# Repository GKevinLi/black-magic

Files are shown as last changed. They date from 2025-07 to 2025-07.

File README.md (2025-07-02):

# Black Magic: A Brushless DC Motor Driver



This is a custom 4S 20A Sensorless BLDC Motor Driver designed for drone motor operation. I haven't had time to make the drone itself because I spent all my time designing this custom PCB instead. Still worth it though.

Features a DRV8323 motor driver chip along with a STM32 microcontroller. Supports full sensorless brushless DC motor operation through PWM input along with current sensing. 

It's called Black Magic because, let's be honest here, I'm messing around with powers beyond my comprehension. I'll be lucky if this thing doesn't blow up the first time I try to plug it in, although I've done my best to make sure that doesn't happen. 20A is still way too much current for someone like me to be playing around with.

This took way longer to make than the other one.... i think its obvious why

## Features
- DRV8323 Motor Controller chip
- STM32 Microcontroller
- USB-C port for programming
- PWM Input
- BEMF Detection through a virtual neutral point
- Current Sensing capabilities
- Voltage Regulator for 3.3v power













## BOM

| Item  | Usage | Source  | Price | Quantity | LCSC ID|
| ----| ----|----|----|----|----|
| 100 uf electrolytic capaciator | Bulk Capacitance | JLCPCB | $4.65 | 20 | C7272127 |
| 10 uf capaciator | Capacitance | JLCPCB | $0.08 | 15 | C19702 |
| 3.3 nf capaciator | Capacitance | JLCPCB | $0.10 | 20 | C26404 |
| 100 nf capaciator | Capacitance | JLCPCB | $0.04 | 40 | C1525 |
| 22 uf capaciator | Bulk Capacitance | JLCPCB | $5.25 | 25 | C5189846 |
| 22 uf capaciator (0603 footprint) | Capacitance | JLCPCB | $0.09 | 10 | C59461 |
| 2.2 uf capaciator | Capacitance | JLCPCB | $0.01 | 5 | C12530 |
| 1 uf capaciator | Capacitance | JLCPCB | $0.02 | 5 | C52923 |
| 47 nf capaciator | Capacitance | JLCPCB | $0.04 | 20 | C272875 |
| Schottky Diode | Preventing reverse current | JLCPCB | $0.10 | 10 | C191023 |
| Red LED | Indication | JLCPCB | $0.03 | 5 | C2286 |
| USB C Receptacle | Programming + Power | JLCPCB | $0.30 | 6 | C2927038 |
| MOSFET | Motor Control | JLCPCB | $8.06 | 30 | C201632 |
| 10 ohm resistor | Resistance | JLCPCB | $0.02 | 30 | C25077 |
| 33k ohm resistor | Resistance | JLCPCB | $0.02 | 30 | C25779 |
| 68k ohm resistor | Resistance | JLCPCB | $0.01 | 30 | C36871 |
| 22k ohm resistor | Resistance | JLCPCB | $0.01 | 5 | C25768 |
| 100k ohm resistor | Resistance | JLCPCB | $0.01 | 5 | C25741 |
| 10k ohm resistor | Resistance | JLCPCB | $0.01 | 20 | C25741 |
| 5.1k ohm resistor | Resistance | JLCPCB | $0.01 | 15 | C25905 |
| 0.01 ohm shunt resistor | Shunt Resistance | JLCPCB | $1.05 | 19 | C393070 |
| 4.7k ohm resistor | Resistance | JLCPCB | $0.01 | 5 | C25900 |
| Button | Button | JLCPCB | $0.42 | 10 | C720477 |
| STM32 | Microcontroller | JLCPCB | $15.86 | 5 | C529355 |
| USBLC6 | USB Data Protector | JLCPCB | $0.96 | 5 | C15999 |
| TLV76133 | Voltage Regulator | JLCPCB | $1.10 | 5 | C7527500 |
| DRV8323 | Motor driver | JLCPCB | $13.29| 5 | C7527500 |
| TPS82130 | Buck Converter | JLCPCB | $6.35 | 5 | C473914 |

Total JLCPCB Assmebly Cost: $73.70

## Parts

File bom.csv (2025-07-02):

Designator | Footprint | Quantity | Value | LCSC ID
C1, C10 | CP_Elec_6.3x7.7 | 2 | 100uf | C7272127
C11, C23, C26 | 0603 | 3 | 10uf | C19702
C12 | 0402 | 1 | 3.3nf | C26404
C13, C19, C20, C21 | 0402 | 4 | 100nf | C1525
C14, C15, C16, C17, C18 | 1812 | 5 | 22uf | C5189846
C2, C7 | 0603 | 2 | 22uf | C59461
C22 | 0402 | 1 | 2.2uf | C12530
C24, C25 | 0402 | 2 | 0u1f | C1525
C3, C6 | 0402 | 2 | 0.1uf | C1525
C4 | 0402 | 1 | 1uf | C52923
C5 | 0402 | 1 | 47nf | C272875
D2, D7 | D_SOD-323 | 2 | D_Schottky | C191023
D6 | 0603 | 1 | LED | C2286
J1 | USB_C_Receptacle_HCTL_HC-TYPE-C-16P-01A | 1 | USB_C_Receptacle_USB2.0_14P | C2927038
J2 | PinSocket_1x03_P2.54mm_Vertical | 1 | Conn_01x03 | Not Assembling
J3 | SolderWire-4sqmm_1x02_P12mm_D3mm_OD6mm | 1 | Conn_01x02 | Not Assembling
J4 | SolderWire-4sqmm_1x03_P12mm_D3mm_OD6mm | 1 | Conn_01x03 | Not Assembling
Q1, Q2, Q3, Q4, Q5, Q6 | VSON-8_3.3x3.3mm_P0.65mm_NexFET | 6 | CSD17577Q3A | C201632
R1, R10, R2, R7, R8, R9 | 0402 | 6 | 10 | C25077
R11, R15, R16, R20, R21, R22 | 0402 | 6 | 33k | C25779
R12 | 0402 | 1 | 68k | C36871
R13 | 0402 | 1 | 22k | C25768
R14 | 0402 | 1 | 100k | C25741
R17, R18, R19, R28 | 0402 | 4 | 10k | C25744
R23 | 0402 | 1 | 5.1k | C25905
R24, R25, R26 | 2512 | 3 | 0.01 | C393070
R27 | 0402 | 1 | 4.7k | C25900
R5, R6 | 0402 | 2 | 5k1 | C25905
SW1, SW3 | SW_Push_SPST_NO_Alps_SKRK | 2 | SW_Push | C720477
U1 | LQFP-48_7x7mm_P0.5mm | 1 | STM32G431CBTx | C529355
U3 | SOT-666 | 1 | USBLC6-2P6 | C15999
U4 | SOT-223-3_TabPin2 | 1 | TLV76133DCY | C7527500
U8 | QFN50P600X600X80-41N415X415 | 1 | DRV8323SRTAT | C2150452
U9 | Texas_SIL0008D_MicroSiP-8-1EP_2.8x3mm_P0.65mm_EP1.1x1.9mm_ThermalVias | 1 | TPS82130 | C473914

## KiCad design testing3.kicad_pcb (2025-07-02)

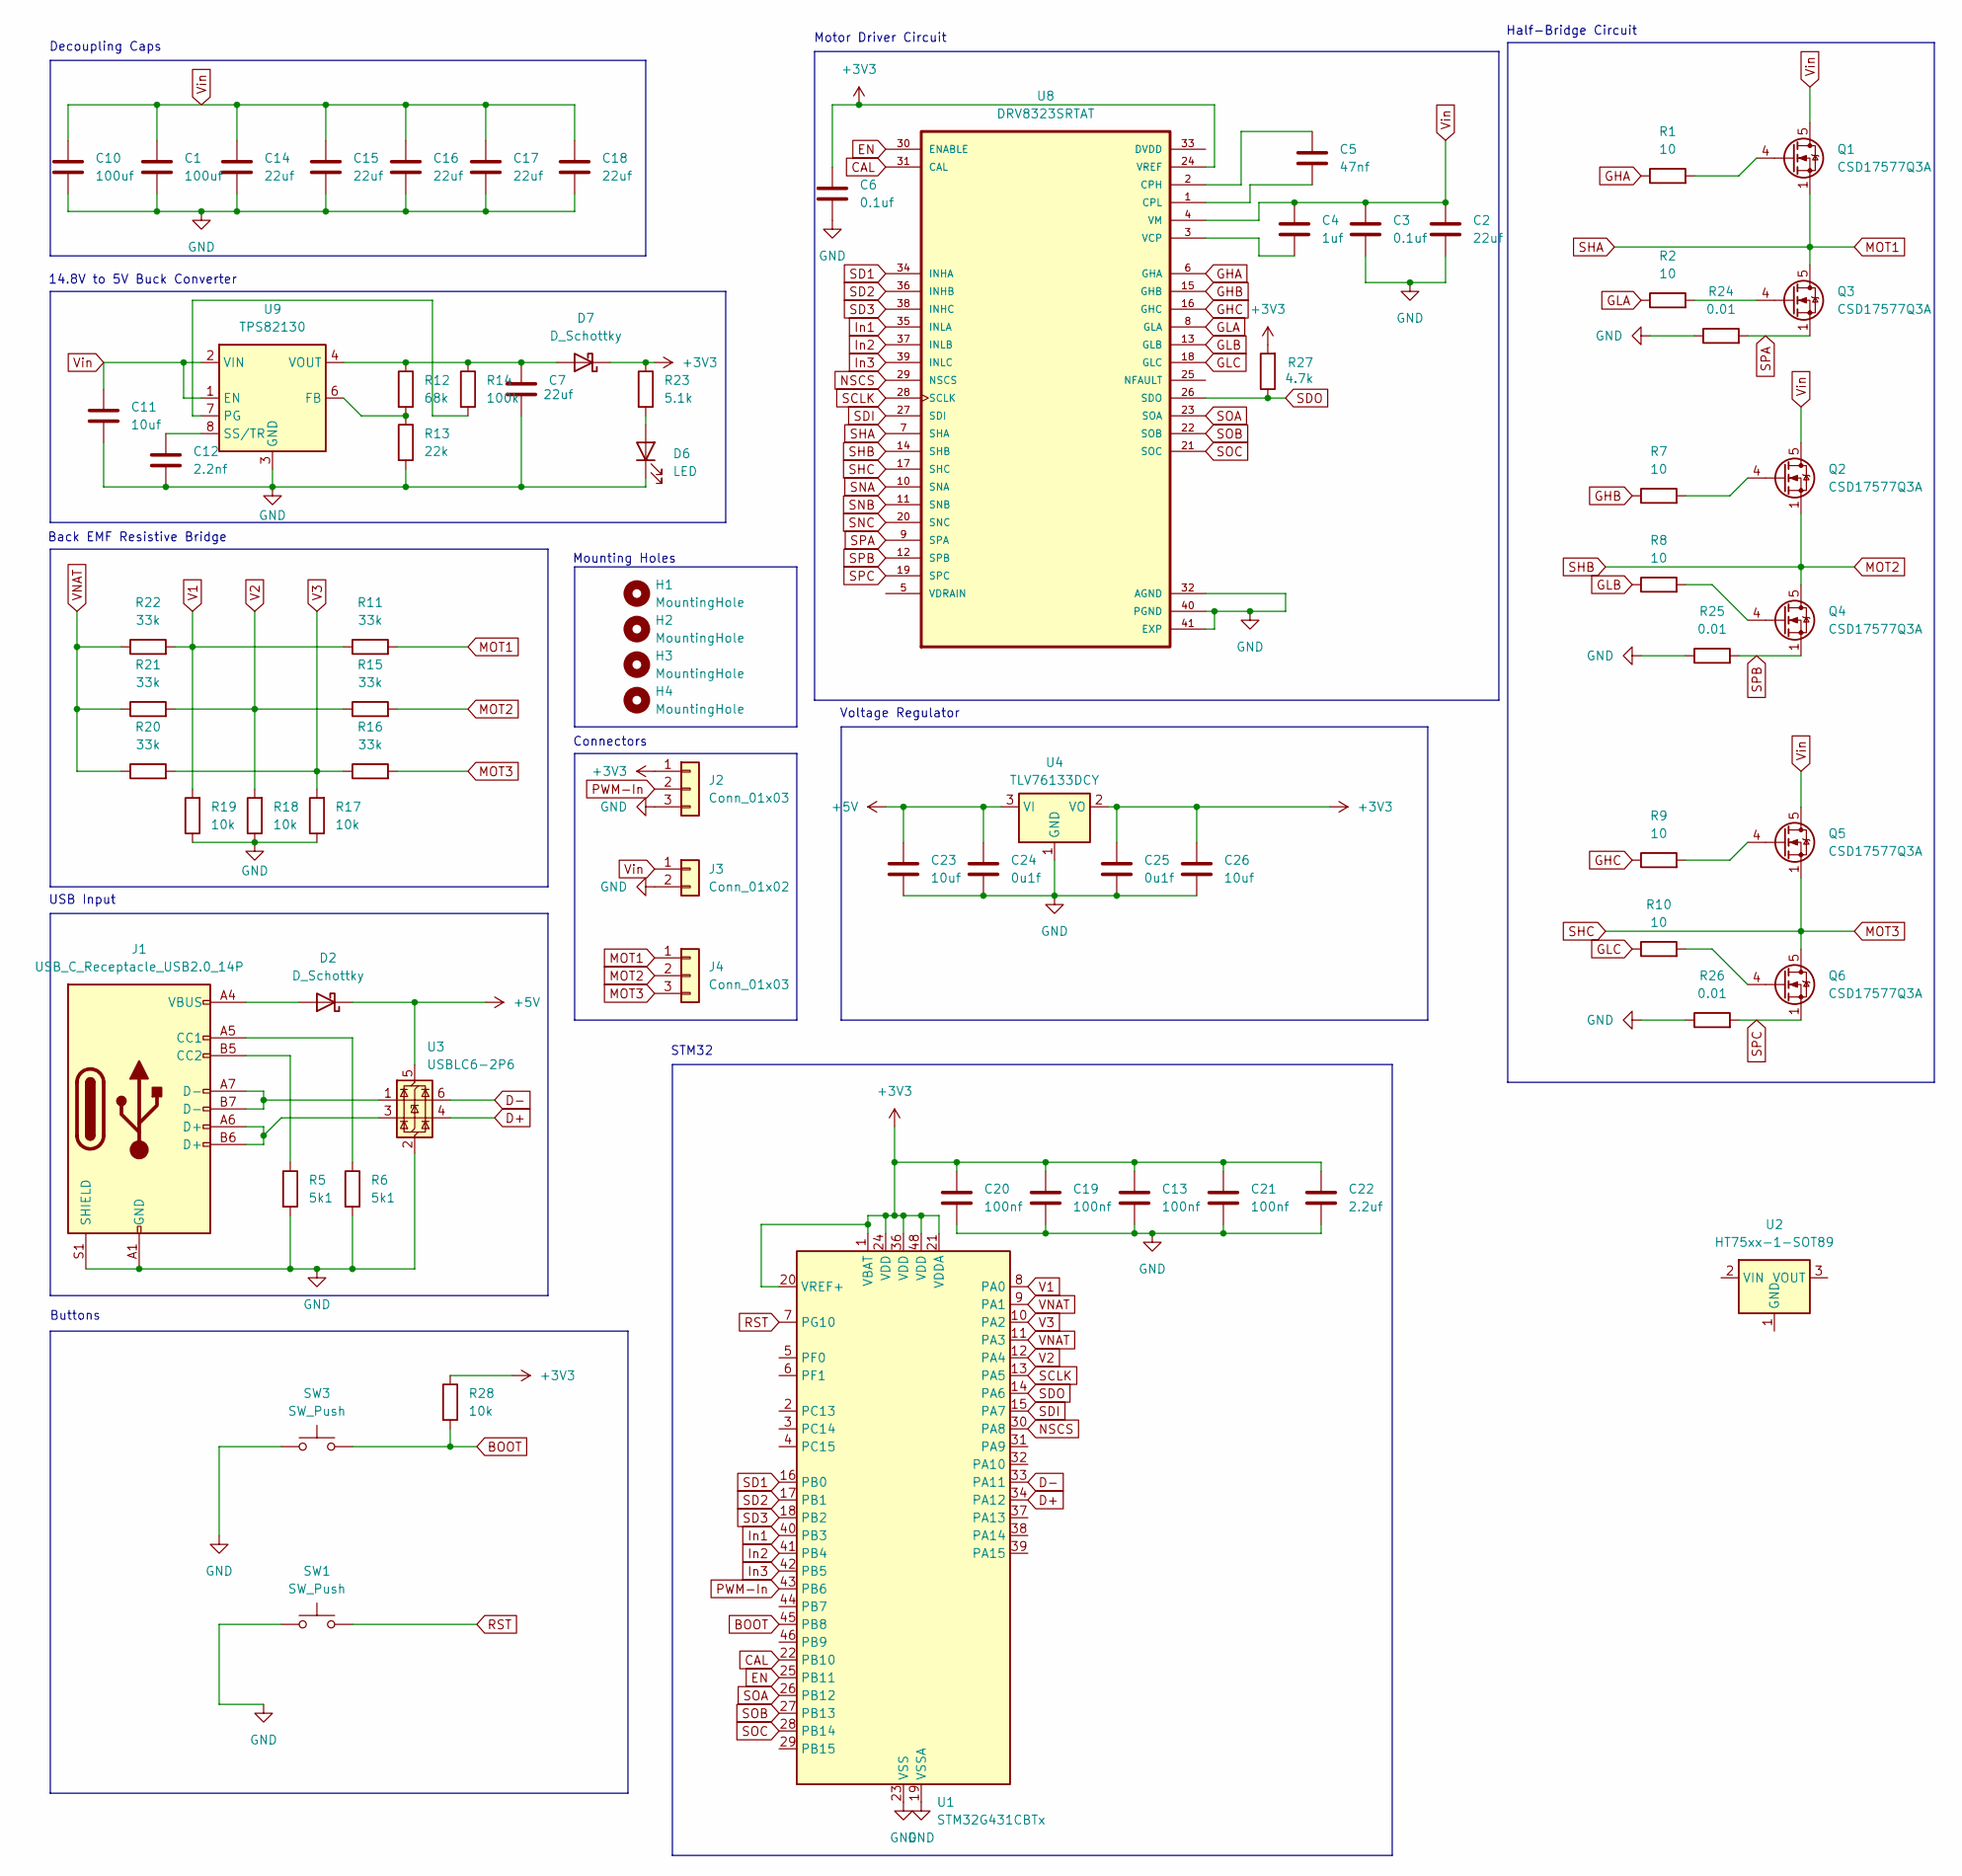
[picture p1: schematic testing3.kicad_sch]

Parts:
C1, C10: 100uf; CP_Elec_6.3x7.7
C2, C7: 22uf; C_0603_1608Metric
C3, C6: 0.1uf; C_0402_1005Metric
C4: 1uf; C_0402_1005Metric
C5: 47nf; C_0402_1005Metric
C11, C23, C26: 10uf; C_0603_1608Metric
C12: 2.2nf; C_0402_1005Metric
C13, C19, C20, C21: 100nf; C_0402_1005Metric
C14, C15, C16, C17, C18: 22uf; C_1812_4532Metric
C22: 2.2uf; C_0402_1005Metric
C24, C25: 0u1f; C_0402_1005Metric
D2, D7: D_Schottky; D_SOD-323
D6: LED; LED_0603_1608Metric
H1, H2, H3, H4: MountingHole; MountingHole_2.1mm
J1: USB_C_Receptacle_USB2.0_14P; USB_C_Receptacle_HCTL_HC-TYPE-C-16P-01A
J2: Conn_01x03; PinSocket_1x03_P2.54mm_Vertical
J3: Conn_01x02; SolderWire-4sqmm_1x02_P12mm_D3mm_OD6mm
J4: Conn_01x03; SolderWire-4sqmm_1x03_P12mm_D3mm_OD6mm
Q1, Q2, Q3, Q4, Q5, Q6: CSD17577Q3A; VSON-8_3.3x3.3mm_P0.65mm_NexFET
R1, R2, R7, R8, R9, R10: 10; R_0402_1005Metric
R5, R6: 5k1; R_0402_1005Metric
R11, R15, R16, R20, R21, R22: 33k; R_0402_1005Metric
R12: 68k; R_0402_1005Metric
R13: 22k; R_0402_1005Metric
R14: 100k; R_0402_1005Metric
R17, R18, R19, R28: 10k; R_0402_1005Metric
R23: 5.1k; R_0402_1005Metric
R24, R25, R26: 0.01; R_2512_6332Metric
R27: 4.7k; R_0402_1005Metric
SW1, SW3: SW_Push; SW_Push_SPST_NO_Alps_SKRK
U1: STM32G431CBTx; LQFP-48_7x7mm_P0.5mm
U2: HT75xx-1-SOT89; SOT-89-3
U3: USBLC6-2P6; SOT-666
U4: TLV76133DCY; SOT-223-3_TabPin2
U8: DRV8323SRTAT; QFN50P600X600X80-41N415X415
U9: TPS82130; Texas_SIL0008D_MicroSiP-8-1EP_2.8x3mm_P0.65mm_EP1.1x1.9mm_T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

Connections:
+3V3: C6.1, C13.1, C19.1, C20.1, C21.1, C22.1, C25.1, C26.1, D7.1 (K), J2.1, R23.1, R27.2, R28.1, U1.1 (VBAT), U1.20 (VREF+), U1.21 (VDDA), U1.24 (VDD), U1.36 (VDD), U1.48 (VDD), U4.2 (VO), U8.24 (VREF)
+5V: C23.1, C24.1, D2.1 (K), U3.5 (VBUS), U4.3 (VI)
BOOT: R28.2, SW3.2, U1.45 (PB8)
CAL: U1.22 (PB10), U8.31 (CAL)
D+: U1.34 (PA12), U3.4 (I/O2)
D-: U1.33 (PA11), U3.6 (I/O1)
EN: U1.25 (PB11), U8.30 (ENABLE)
GHA: R1.1, U8.6 (GHA)
GHB: R7.1, U8.15 (GHB)
GHC: R9.1, U8.16 (GHC)
GLA: R2.1, U8.8 (GLA)
GLB: R8.1, U8.13 (GLB)
GLC: R10.1, U8.18 (GLC)
GND: C1.2, C2.2, C3.2, C6.2, C7.2, C10.2, C11.2, C12.2, C13.2, C14.2, C15.2, C16.2, C17.2, C18.2, C19.2, C20.2, C21.2, C22.2, C23.2, C24.2, C25.2, C26.2, D6.1 (K), J1.A1 (GND), J1.A12 (GND), J1.B1 (GND), J1.B12 (GND), J1.S1 (SHIELD), J2.3, J3.2, R5.2, R6.2, R13.2, R17.1, R18.1, R19.1, R24.1, R25.1, R26.1, SW1.1, SW3.1, U1.19 (VSSA), U1.23 (VSS), U1.35 (VSS), U1.47 (VSS), U3.2 (GND), U4.1 (GND), U8.32 (AGND), U8.40 (PGND), U8.41 (EXP), U9.3 (GND), U9.9 (GND)
In1: U1.40 (PB3), U8.35 (INLA)
In2: U1.41 (PB4), U8.37 (INLB)
In3: U1.42 (PB5), U8.39 (INLC)
MOT1: J4.1, Q1.1 (S), Q1.2 (S), Q1.3 (S), Q3.5 (D), R11.2, U8.7 (SHA)
MOT2: J4.2, Q2.1 (S), Q2.2 (S), Q2.3 (S), Q4.5 (D), R15.2, U8.14 (SHB)
MOT3: J4.3, Q5.1 (S), Q5.2 (S), Q5.3 (S), Q6.5 (D), R16.2, U8.17 (SHC)
NSCS: U1.30 (PA8), U8.29 (NSCS)
unnamed: D2.2 (A), J1.A4 (VBUS), J1.A9 (VBUS), J1.B4 (VBUS), J1.B9 (VBUS)
unnamed: D6.2 (A), R23.2
unnamed: C7.1, D7.2 (A), R12.1, R14.1, U9.4 (VOUT), U9.5 (VOUT)
unnamed: J1.A5 (CC1), R6.1
unnamed: J1.B5 (CC2), R5.1
unnamed: J1.A6 (D+), J1.B6 (D+), U3.3 (I/O2)
unnamed: J1.A7 (D-), J1.B7 (D-), U3.1 (I/O1)
unnamed: Q1.4 (G), R1.2
unnamed: Q2.4 (G), R7.2
unnamed: Q3.4 (G), R2.2
unnamed: Q4.4 (G), R8.2
unnamed: Q5.4 (G), R9.2
unnamed: Q6.4 (G), R10.2
unnamed: C5.1, U8.2 (CPH)
unnamed: C5.2, U8.1 (CPL)
unnamed: C4.2, U8.3 (VCP)
unnamed: R12.2, R13.1, U9.6 (FB)
unnamed: R14.2, U9.7 (PG)
unnamed: C12.1, U9.8 (SS/TR)
PWM-In: J2.2, U1.43 (PB6)
RST: SW1.2, U1.7 (PG10)
SCLK: U1.13 (PA5), U8.28 (SCLK)
SD1: U1.16 (PB0), U8.34 (INHA)
SD2: U1.17 (PB1), U8.36 (INHB)
SD3: U1.18 (PB2), U8.38 (INHC)
SDI: U1.15 (PA7), U8.27 (SDI)
SDO: R27.1, U1.14 (PA6), U8.26 (SDO)
SNA: U8.10 (SNA)
SNB: U8.11 (SNB)
SNC: U8.20 (SNC)
SOA: U1.26 (PB12), U8.23 (SOA)
SOB: U1.27 (PB13), U8.22 (SOB)
SOC: U1.28 (PB14), U8.21 (SOC)
SPA: Q3.1 (S), Q3.2 (S), Q3.3 (S), R24.2, U8.9 (SPA)
SPB: Q4.1 (S), Q4.2 (S), Q4.3 (S), R25.2, U8.12 (SPB)
SPC: Q6.1 (S), Q6.2 (S), Q6.3 (S), R26.2, U8.19 (SPC)
V1: R11.1, R19.2, R22.2, U1.8 (PA0)
V2: R15.1, R18.2, R21.2, U1.12 (PA4)
V3: R16.1, R17.2, R20.2, U1.10 (PA2)
VNAT: R20.1, R21.1, R22.1, U1.9 (PA1), U1.11 (PA3)
Vin: C1.1, C2.1, C3.1, C4.1, C10.1, C11.1, C14.1, C15.1, C16.1, C17.1, C18.1, J3.1, Q1.5 (D), Q2.5 (D), Q5.5 (D), U8.4 (VM), U9.1 (EN), U9.2 (VIN)

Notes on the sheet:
Voltage Regulator
Decoupling Caps
Mounting Holes
USB Input
Connectors
Buttons
Back EMF Resistive Bridge
Motor Driver Circuit
STM32
14.8V to 5V Buck Converter
Half-Bridge Circuit

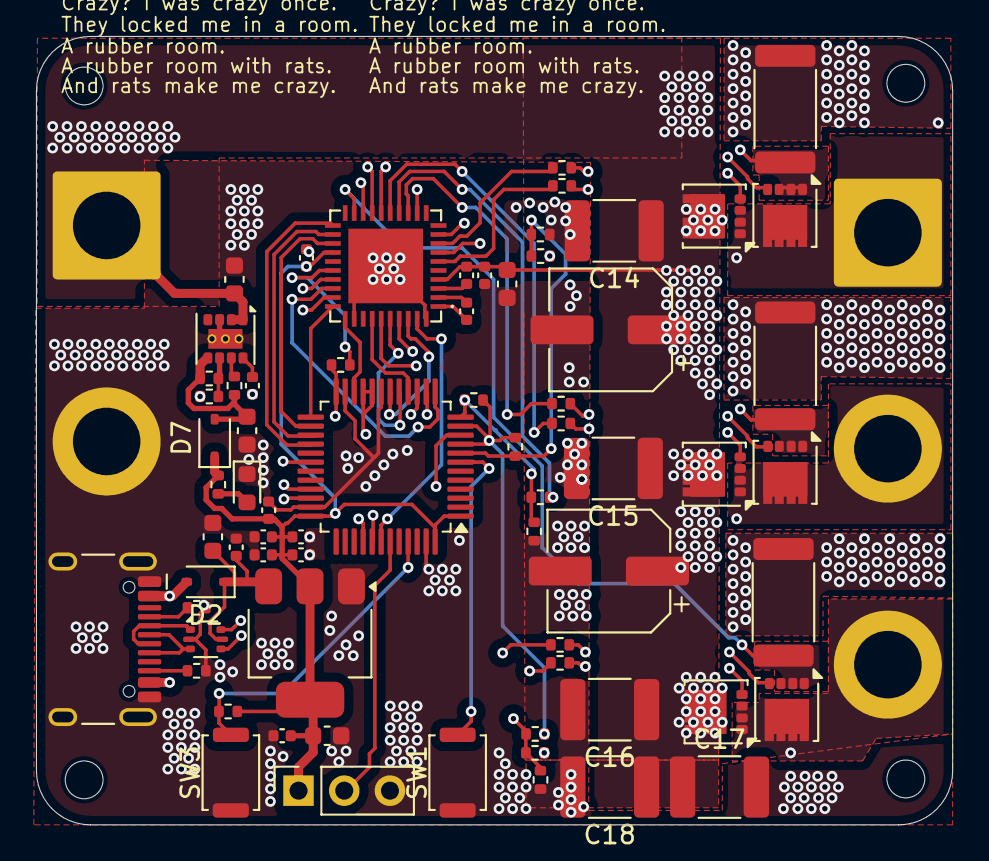
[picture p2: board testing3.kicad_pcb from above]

Board: 4 copper layers, 50.9 x 43.8 mm, 74 parts (0 on the bottom side), 59 nets.

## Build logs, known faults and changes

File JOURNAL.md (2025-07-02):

---
title: "black magic"
author: "kevin"
description: "brushless motor controller"
created_at: "2025-06-11"
---
Total time spent: 35 hours

# June 11: figuring stuff out

Did some research on BLDC motor drivers in general and figured out what I needed. Figured out all the basic parts for a half-bridge circuit and made a quick schematic of one in KiCad. I also began looking into parts for the gate drivers and the MOSFETs specifically.

Turns out this project is actually quite complicated, involves high amounts of current, and is pretty ill-advised for a young child like me. But fuck it we ball



**Total time spent: 4h**

# June 12: parts and stuff

Spent some time looking for good components to use as part of the motor driver circuit. Eventually found some reasonably cheap MOSFETs and gate drivers that fit my requirements. 
Also decided on using the ATMega328P as the microcontroller, as it's pretty cheap and also fits all of the requirements I need.

Hopefully going to get started on the schematic tommorrow, this is already 10x more painful than the other board i made

**Total time spent: 3h**

# June 13: sch'matic

Did some schematic stuff. Copied over the USB-C port schematic from my other project and added the ATMega328P schematic. Also made a schematic for the CP2102 USB to UART bridge because the ATMega doesn't have built in USB support. Added a schematic for the 14.8v to 5v buck converter to power the Arduino straight from the battery.







**Total time spent: 2h**

# June 14: (traumatic war flashbacks)

Began working on the PCB layout. Managed to get all of my current schematic layed out, but I'm still planning on adding some other stuff. Also added some preliminary ground, Vin, M1, M2, and M3 copper pours. I decided to use a 4-layer board due to the convenience of routing as well as to reduce EMI.



**Total time spent: 4h**

# June 15: other stuff i guess

Completed the schematic by adding some extra stuff I needed for the layout. Basically just added some bulk capacitance, the back EMF resistive bridge, and some mounting holes as well as the PWM input pins. Also worked on the routing a bit more today, mostly by adding the new stuff from the schematic and cleaning up the traces a bit.



**Total time spent: 3h**

# June 18: well it's done, time for design review ig

finished the pcb layout and the schematic, so i'm gonna upload this to reddit for a design review. last time I did this I got a lot of rlly helpful suggestions, so hopefully this time i can find a bunch of ways to improve this design. I'm still feeling rather iffy on this design, it seems a bit weird and there are some things I wanted to add (current sensing) but didn't get the space to, so i'll ask about that as well.




**Total time spent: 3h**

# June 19: rethinking my entire worldview because of what some strangers said to me on the internet

welp its time for a redesign

based on much of the advice on reddit, I have decided that my current design sucks ass. Therefore, I have decided to restart completely and begin redesigning the whole thing, starting from the motor outputs and the MOSFETs. I have also decided to include current sensing because SCOPE CREEP IS NOT REAL AND CANNOT HURT ME.

I have made the decision to change my design from using three seperate half-bridge drivers to one big fancy DRV8323 motor driver. This is because it saves a bunch of space, money (from supporting components), and has current sensing integrated into the driver, so I don't need any extra components for that. 

Lots of datasheets today! I'm having fun! I'm having fun! I'm having fun!

**Total time spent: 5h**

# June 20: beginning the redesign

Did a bunch of layout work today and added the DRV8323 schematic as well as the new mosfet schematics. I found some good shunt resistors for current sensing and added those to the design as well. This redesign addresses a bunch of the issues present in the old design, and it's going ok so far????



**Total time spent: 3h**

# June 21: cahnges

Officially decided to swap out the ATMega328p to a STM32 chip. Just looked at the specs and the STM32s are so much better it isn't even a close comparison. Because of this, I also now don't need a USB to UART bridge because the STM32 has built in USB! It's perfect! 

Spent a while reading the datasheet just to see if the STM32 had everything I needed (pwm outputs, enough comparators for back EMF, etc) and the best pin layout to use for it.

**Total time spent: 2h**

# June 22: the work continues

Placed the DRV8323 motor driver and connected all the tracks to the motor drivers. Also redid the schematics (changed the buck converter to output 3.3v and added a linear voltage regulator)
Didn't do much today so thats about it

**Total time spent: 1h**

# June 26: this is the grind that never ends

Spent a bunch of time today adding the STM32 to the board, connecting all the tracks for those, and just adding everything else that needed to be added. Layout is basically done now. I'm tired man



**Total time spent: 4h**

# June 29: Finishing touches + another design review

Decided to submit it to Reddit again for another design review. This design should be a lot better than the last one, so hopefully there's less stuff to change. I'll have to wait and see...

**Total time spent: 1h**
